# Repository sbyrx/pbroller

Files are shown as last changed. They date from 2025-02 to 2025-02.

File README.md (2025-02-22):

# PBRoller
Tired of manually mixing your natural peanut butter? Tired of getting oil everywhere and making a mess? Look no further! Simply place your peanut butter jar on the PBRoller, leave it for a few hours, and come back to perfectly mixed peanut butter!



Post your reviews and makes on [MakerWorld](https://makerworld.com/en/models/1134964#profileId-1135977) and [Printables](https://www.printables.com/model/1201341-pbroller-peanut-butter-mixer)

## Build Instructions
### Parts List
Before you get started, here are all the things you'll need to buy to build your very own PBRoller. For reference I've included links to the products I purchased:
1. Raspberry Pi Pico
    - Source from your local [Raspberry Pi authorized reseller](https://www.raspberrypi.com/resellers/)
1. [Easy Driver Stepper Motor Controller](https://ca.robotshop.com/products/easydriver-stepper-motor-controller-a3967)
1. [NEMA 17 Stepper Motor (12V and 350mA)](https://www.pishop.ca/product/stepper-motor-nema-17-size-200-stepsrev-12v-350ma/)
1. [NEMA 17 Stepper Motor Mount](https://a.co/d/4L3NoFJ)
1. 12V Power Supply (I use one I had laying around)
1. [M2x4mm Screws](https://www.amazon.ca/dp/B0C38YFL3D)
1. [M2x6mm Screws](https://www.amazon.ca/dp/B0C38YFL3D)
1. [M4x8mm Screws](https://www.amazon.ca/dp/B0C38YFL3D)
1. [M2x4mm Heat Set Nuts (3.2mm outer diameter)](https://www.amazon.ca/dp/B0CNRSJ1B2)
1. [M4x4mm Heat Set Nuts (5.2mm outer diameter)](https://www.amazon.ca/dp/B0CNRSJ1B2)
1. [Rocker Switch](https://abra-electronics.com/electromechanical/switches/rocker-switches/com-08837-rocker-switch-spst-right-angle-com-08837.html)
1. [12V DC Barrel Connector (11mm outer diameter)](https://www.amazon.ca/dp/B08SJM2G52)
1. [Heat sinks](https://www.amazon.ca/dp/B0814V66JV) (optional, but the Easy Driver can get pretty hot)
1. [Skateboard Bearings](https://a.co/d/eMN2Fxm)
1. [8mm metal rod](https://a.co/d/23PNJWb)
1. Solder and wire
1. Heat shrink tube

### 3D Printed Parts
Print all parts with 0.2mm layer height and 15% infill. I recommend printing the gears with 4 wall loops for some added strength.

I've included [Bambu Studio Project file](docs/models/pbroller.3mf) with all parts laid out on two build plates and configured.

|Model|Image|Details|
|-----|-----|---|
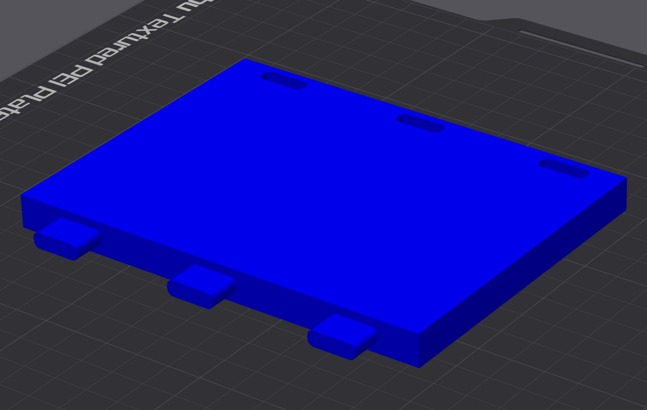
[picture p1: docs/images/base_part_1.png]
Rendering of the Base Part 1
|[Base Part 1](docs/models/base_part_1.stl)||Base of the PBRoller. Connects to the second part of the base using some pegs. The left side slots into the holes.<br><br>**Print Orientation**: Right side up<br>**Quantity**: 1<br>**Supports**: Yes|
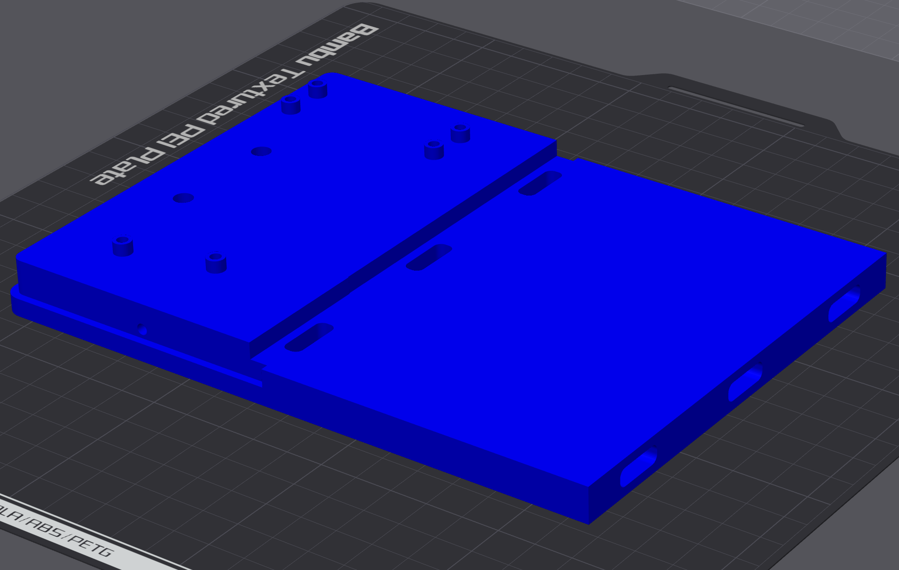
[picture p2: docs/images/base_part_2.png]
Rendering of the Base Part 2
|[Base Part 2](docs/models/base_part_2.stl)||Second half of the PBRoller base. Contains holes for heat set nuts for mounting the stepper motor, Pi Pico, Easy Driver, and for attaching the cover. The right side slots into the holes.<br><br>**Print Orientation**: Right side up<br>**Quantity**: 1<br>**Supports**: No|
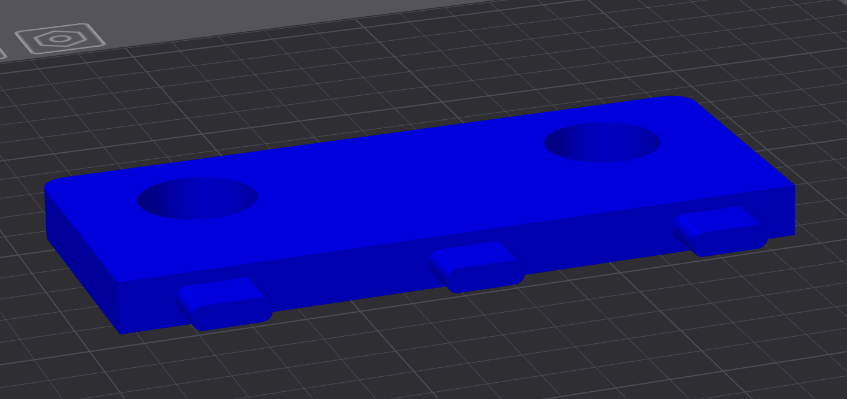
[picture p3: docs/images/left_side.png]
Rendering of the Left Side
|[Left Side](docs/models/left_side.stl)||The left bracket of the PBRoller, which slots into the first base part using the pegs. Skateboard bearings are pressed into the two large openings to hold the rollers.<br><br>**Print Orientation**: Right side up<br>**Quantity**: 1<br>**Supports**: Yes|
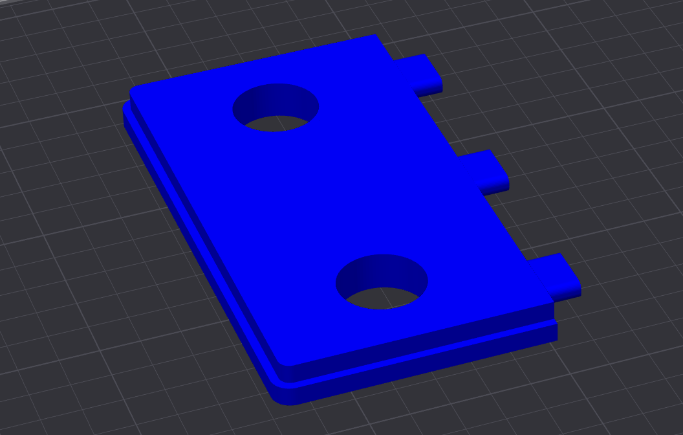
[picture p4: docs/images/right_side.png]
Rendering of the Right Side
|[Right Side](docs/models/right_side.stl)||Right bracket of the PBRoller, which slots into the second base part using the pegs. Skateboard bearings are pressed into the two large openings to hold the rollers.<br><br>**Print Orientation**: Right side up<br>**Quantity**: 1<br>**Supports**: Yes|
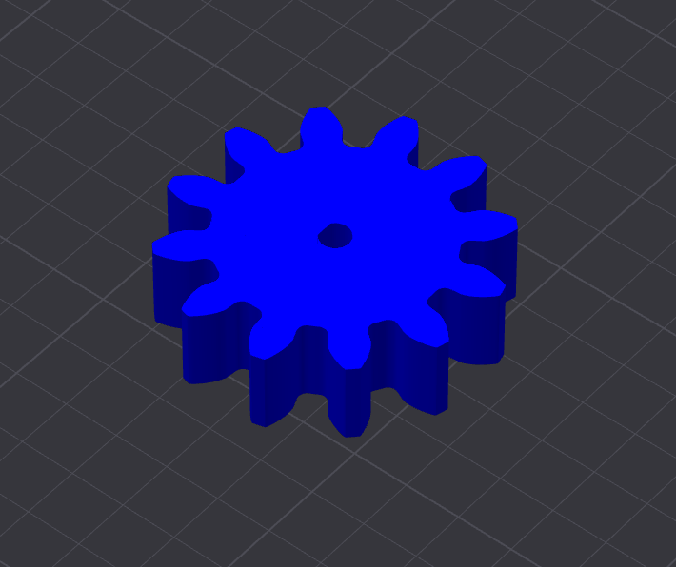
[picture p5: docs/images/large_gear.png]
Rendering of the Large Gear
|[Large Gear](docs/models/large_gear.stl)||Press fits to the stepper motor and drives the two smaller gears which drive the rollers<br><br>**Print Orientation**: Right side up<br>**Quantity**: 1<br>**Supports**: No|
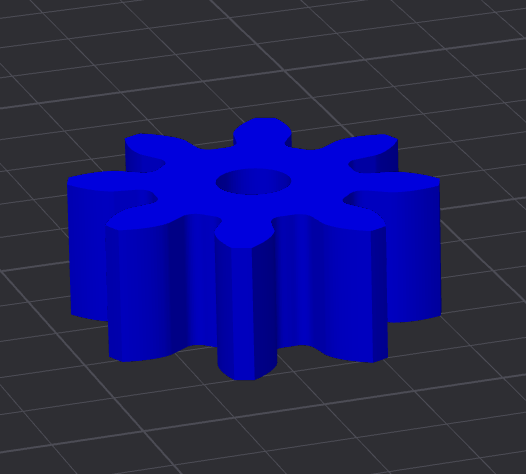
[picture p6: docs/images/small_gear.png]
Rendering of the Small Gear
|[Small Gear](docs/models/small_gear.stl)||The two small gears are press fit onto the 8mm rod and drive the rollers.<br><br>**Print Orientation**: Right side up<br>**Quantity**: 2<br>**Supports**: No|
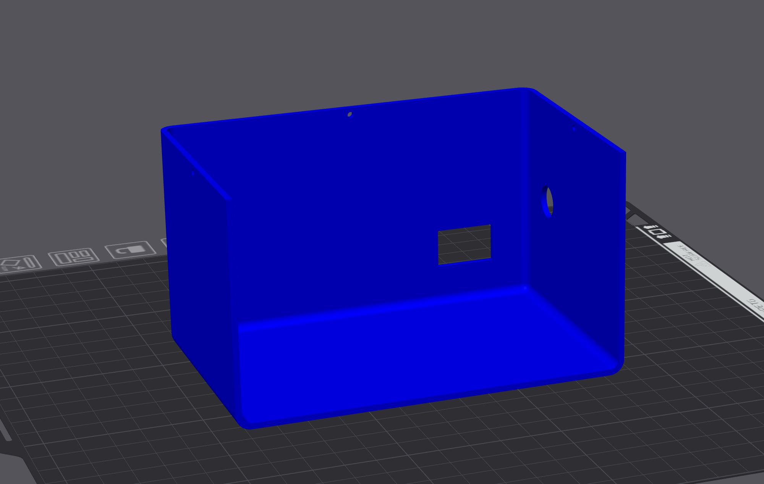
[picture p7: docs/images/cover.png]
Rendering of the Cover
|[Cover](docs/models/cover.stl)||Covers the electronics and stepper motor. Attaches to the base using 3 M2 screws. Has holes for the rocker switch and barrel connector.<br><br>**Print Orientation**: Up side down<br>**Quantity**: 1<br>**Supports**: No|

### Assembly
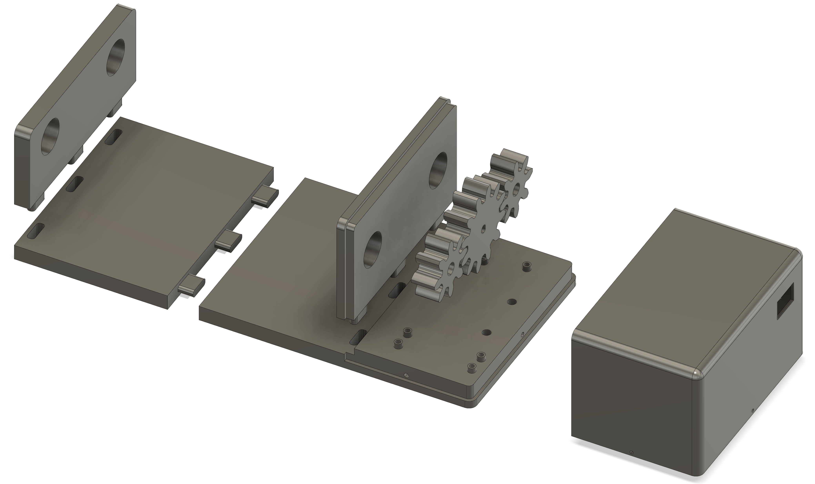
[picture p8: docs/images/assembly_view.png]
PB Roller Assembly View


Begin by setting the M2 heat set nuts into the three holes in the sides and back of Base Part 2 where the Cover attaches. Continue by setting the other M2 heat set nuts which hold the electronics, and the two M4 heat set nuts which the stepper motor mount attaches to.

Connect the two halves of the base together. You may have to clean up/file the pegs a little to get a good fit. Press the skateboard bearings into the Left Side and Right Side before attaching them to the base by by pressing them into their respective slots (again, you may need to clean up the pegs to get a good fit).

Cut the 8mm rod into two lengths of 21cm. Press a small gear onto the end of each (they're a tight fit - you may need to ream the gears out a little with a drill bit or a file). Slide the rods through the bearings and into place. Make sure there's sufficient clearance between the gear and the side so that nothing is rubbing and the rollers are spinning freely. Apply a small dab of super glue to attach the metal rod to each bearing.

Press the large gear onto the end of the stepper motor. Attach the stepper motor to the mount and attach the mount to the base using the M4 screws. Now it's time to wire everything up!

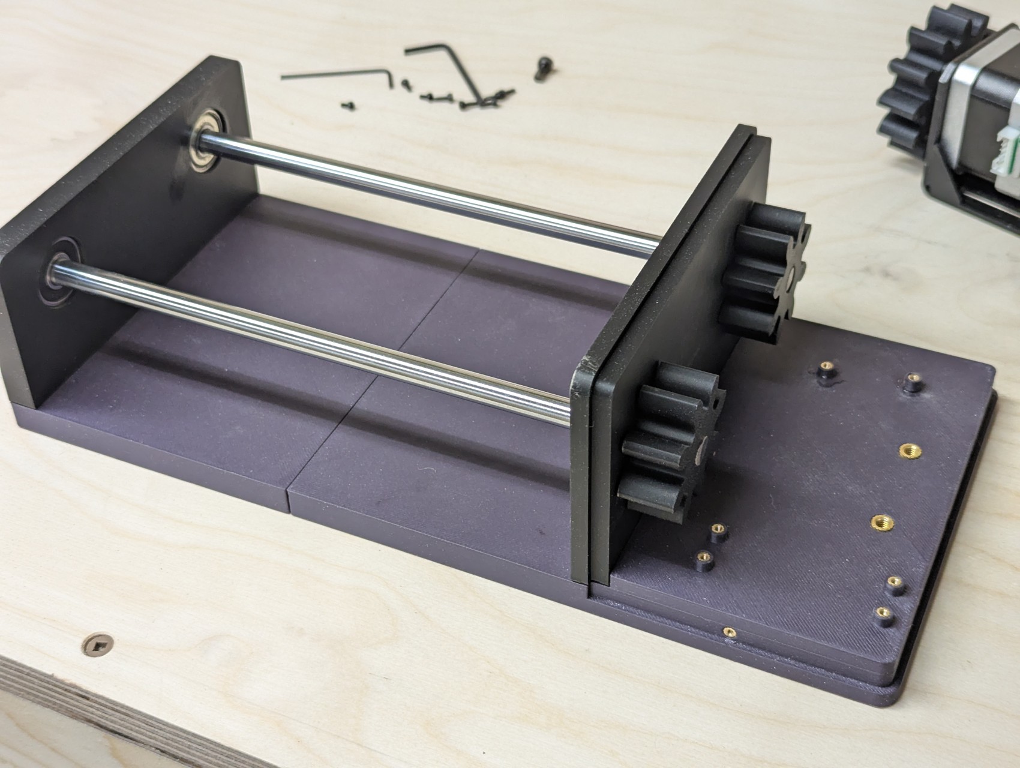
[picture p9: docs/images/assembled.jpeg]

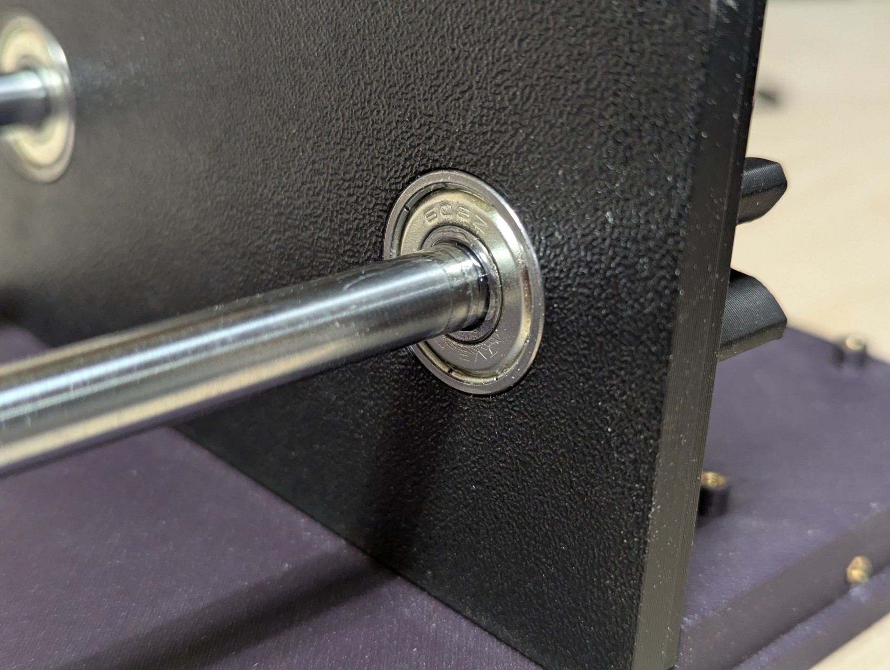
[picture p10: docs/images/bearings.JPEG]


### Electronics
Since the Pico uses 3.3V logic, the first thing you should do is switch the Easy Driver to use 3.3V logic as well by soldering SJ2 closed (placing a small glob of solder on the two pads on the bottom left hand corner of the board where it's written "5V/3V"). You can confirm you've done this correctly by measuring the voltage across the +5V Output and GND, which should now be 3.3V.

Next, wire the Easy Driver to the Pico as follows:
1. DIR -> GP15
1. STEP -> GP14
1. GND -> GND (Pin 18)
1. SLP -> GP13 

The Easy Driver has a 5V (3.3V) output which I'm taking advantage of to power the Pico. Wire the 5V (now 3.3V) output on the Easy Driver to VSYS on the Pico, and GND to GND.

Mount the barrel connector to the cover using the nut it comes with. Wire the switch in series on the positive side of the power leads coming off the barrel connector, and snap the switch into the cover. Then, solder the positive and negative leads to PWR IN and GND on the Easy Driver. 

**Note:** I've opted to solder headers to each board and make the connections using jumper wires. That being said, it's important to make sure the PWR IN and stepper motor connections are solid or you risk blowing up the Easy Driver. Always power off the Easy Driver before plugging/unplugging the stepper motor!

Mount the Pico and Easy Driver to the base using M2 screws. Plug in the stepper motor to the Easy Driver. Now it's time to program the Pico!

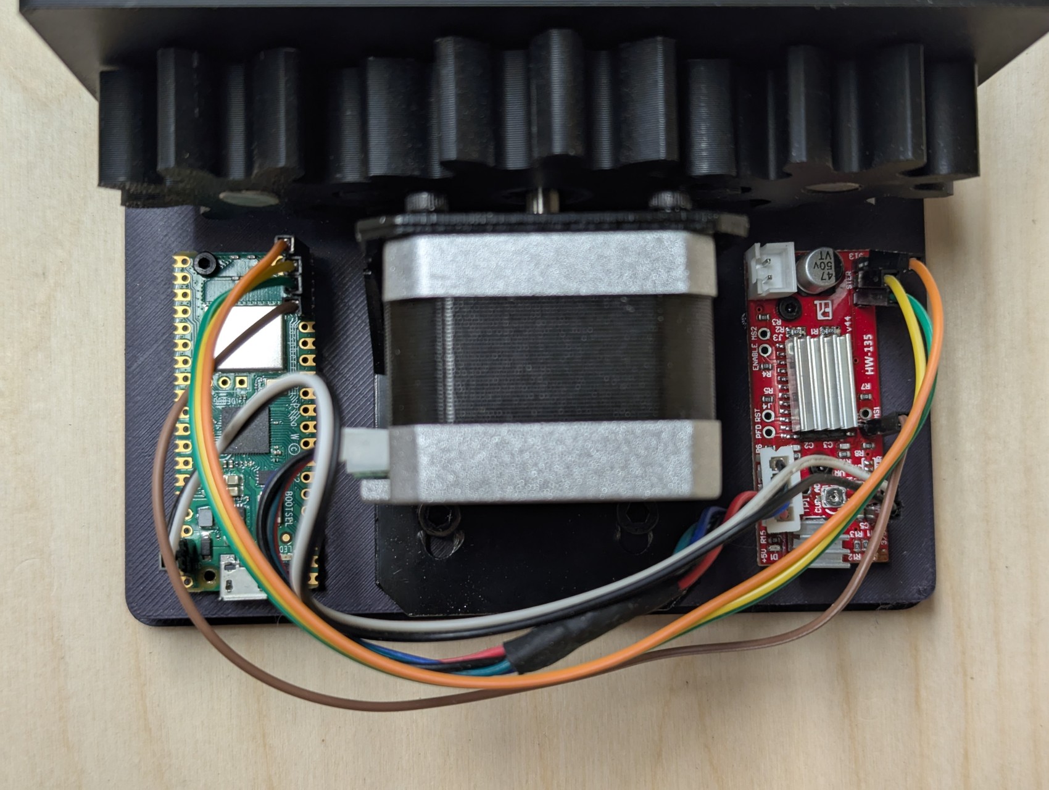
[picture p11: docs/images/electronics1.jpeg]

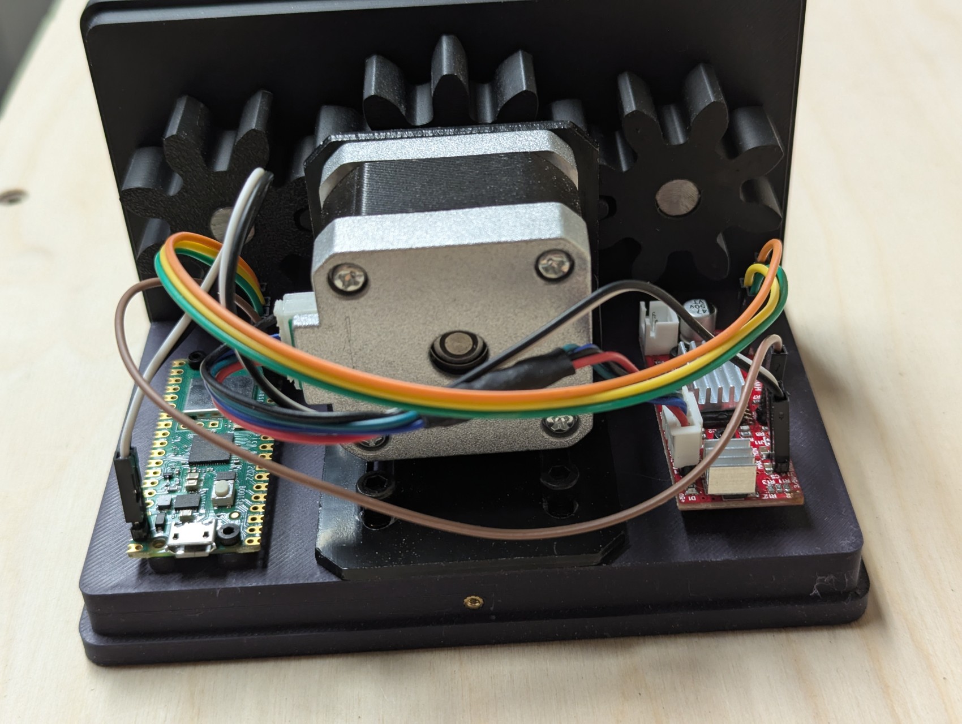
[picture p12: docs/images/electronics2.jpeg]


### Code

The PBRoller software for the Pico is written in Micropython. Follow the [instructions here](https://www.raspberrypi.com/documentation/microcontrollers/micropython.html) to flash Micropython onto your board.

I also recommend setting up a Visual Studio project and installing the [MicroPico extension](https://github.com/paulober/MicroPico) to copy the code to the board.

#### main.py

This is the Micropython code which runs on the Pico and interfaces with the Easy Driver to turn the stepper motor and roll the peanut butter jar. It's only a couple of lines of code and simply spins the jar 180 degrees, sleeps for 30 seconds, then repeats. In my testing I found this method of pausing and spinning to give the best mix.

To run the code on your Pico, connect your Pico to your computer, and wait for VSCode to show "Pico Connected" in the bottom toolbar. Then right click on `main.py` and click "Upload current file to Pico".

You should now be all set! Power everything up and let the good times roll.

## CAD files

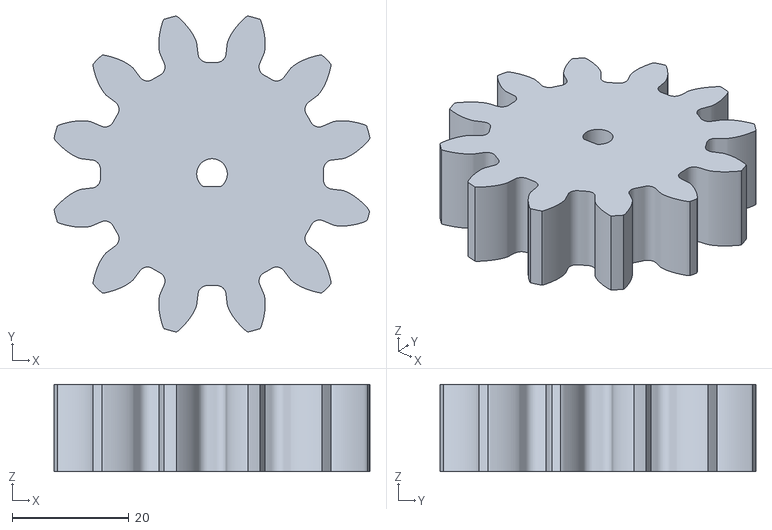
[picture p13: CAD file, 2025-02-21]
docs/models/large_gear.stl
54.2 x 54.2 x 15.0

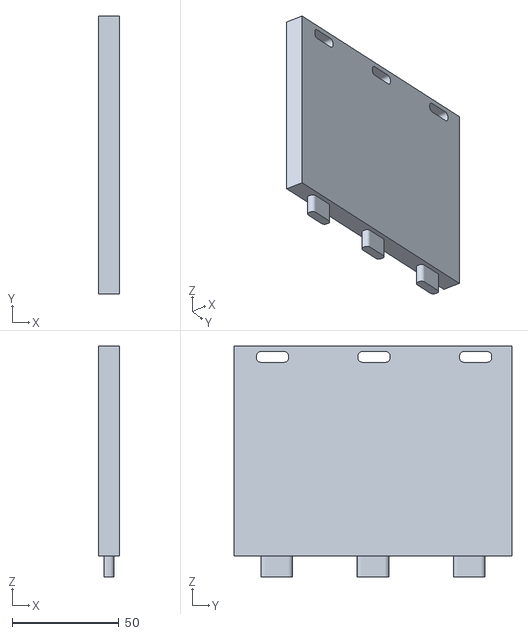
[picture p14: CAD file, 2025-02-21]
docs/models/base_part_1.stl
10.0 x 130.0 x 107.8

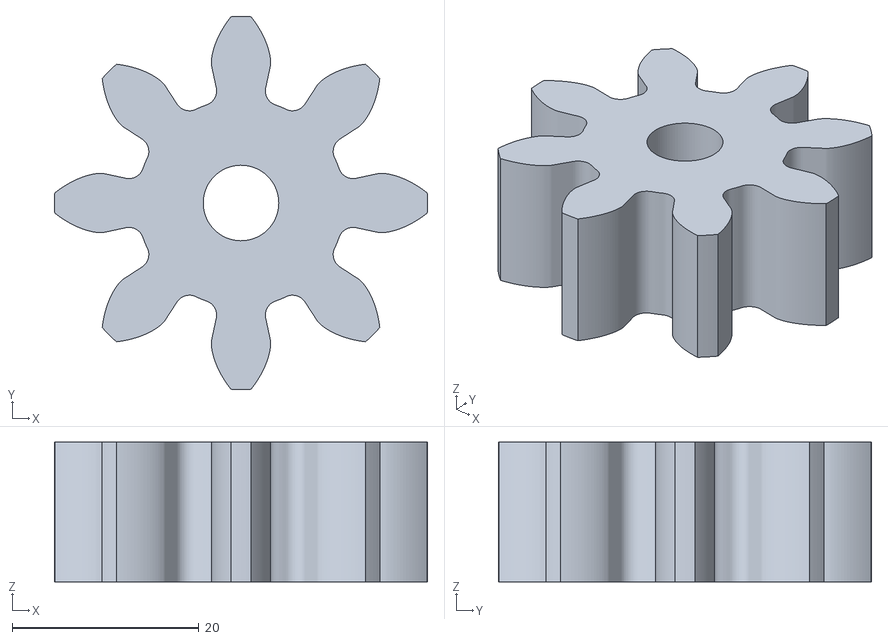
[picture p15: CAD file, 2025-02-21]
docs/models/small_gear.stl
40.0 x 40.0 x 15.0

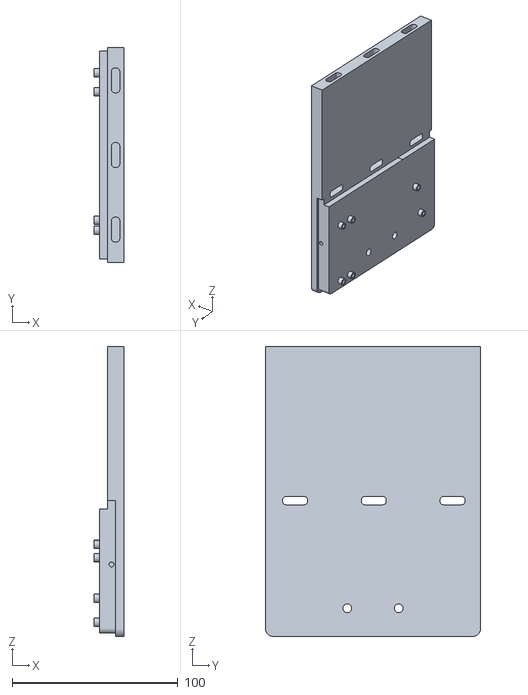
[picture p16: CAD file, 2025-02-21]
docs/models/base_part_2.stl
18.0 x 130.0 x 175.0

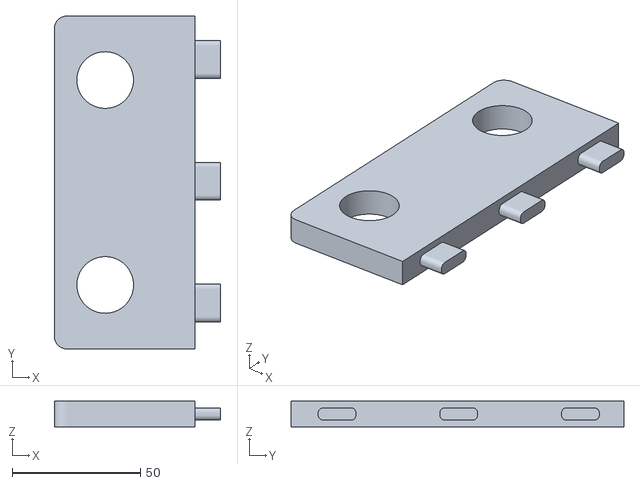
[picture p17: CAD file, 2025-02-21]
docs/models/left_side.stl
65.0 x 130.0 x 10.0

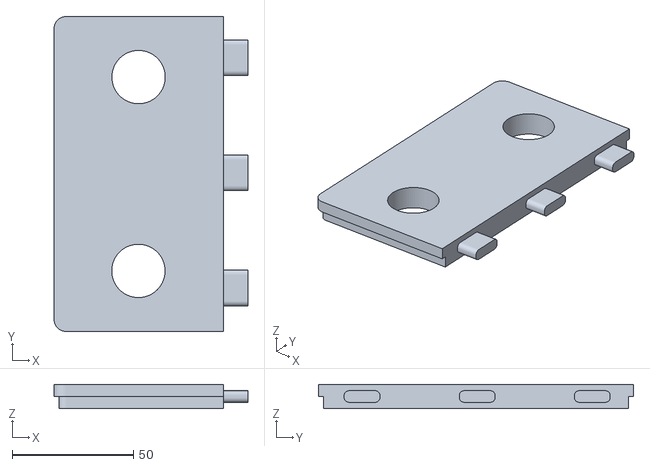
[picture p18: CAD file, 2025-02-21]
docs/models/right_side.stl
80.0 x 130.0 x 10.0

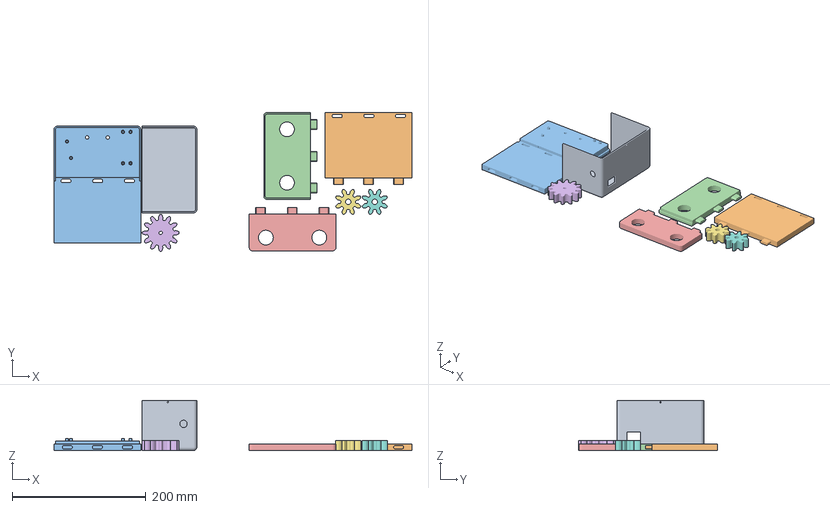
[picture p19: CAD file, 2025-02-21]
docs/models/pbroller.3mf
536.1 x 207.8 x 75.0 mm
cover.stl
base_part_1.stl
base_part_2.stl
right_side.stl
left_side.stl
large_gear.stl
small_gear.stl x 2

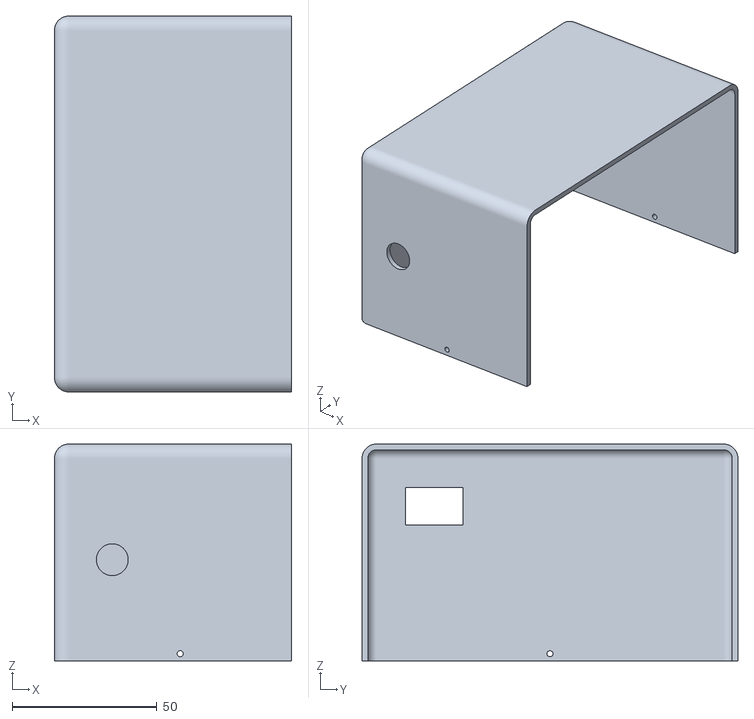
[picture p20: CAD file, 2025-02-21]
docs/models/cover.stl
82.0 x 130.0 x 75.0

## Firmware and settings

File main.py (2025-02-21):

from machine import Pin
import time

led = Pin('LED', Pin.OUT)
dir = Pin(15, Pin.OUT)
step = Pin(14, Pin.OUT)
sleep = Pin(13, Pin.OUT)

led.low()
sleep.low()
dir.low()
step.low()

while True:
    sleep.high()
    for x in range(3200):
        step.value(1)
        time.sleep_ms(1)
        step.value(0)
        time.sleep_ms(1)
        if x % 100 == 0:
            led.toggle()
    sleep.low()
    led.high();
    time.sleep(30)
